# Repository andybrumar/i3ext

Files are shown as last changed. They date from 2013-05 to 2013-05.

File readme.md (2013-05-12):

Prusa i3 Extruder
-----------------

This is a derivative of Kliment's excellent work on his 'i3ext' project for
the Prusa i3 3D printer.

I have modified it to work with jhead hotends (potentially dual extrusion, 
if stacked vertically - option now available), MK7-compatible hobbed pulleys, and
variable mount hole spacings.  Example models are available for viewing in
the /STLs folder.

The extruder requires:

* NEMA17 stepper motor
* 625zz bearings (2 - for large gear axle)
* ~75mm M5 threaded rod (1 - for large gear axle)
* M5 nyloc (2 - for large gear axle)
* M5 nut (1 - for large gear axle)
* MK7 hobbed pulley (1 - Makerbot, TrinityLabs, etc)
* M3 nut (5 - 4-motor mount, 1-small gear)
* 6mm M3 screw (1 - small gear)

RP one of each:

* main_block_v2.scad -OR- main_block_v2_kliment.scad
* idler.scad
* large_gear, small_gear from gears.scad -OR- gears-kliment.scad
* fan_mount.scad

Kliment's variant uses smaller gear diameters, which makes the dual extruder 
less tall.

I have about 15 hours of printing with this extruder (non-Kliment) and it's been
reliable so far.

Build
=====

A great photo of how the assembly goes together can be found here:

http://www.flickr.com/photos/borgnamarco/8480383523/

Also check out the other photos in this photostream:

http://www.flickr.com/photos/borgnamarco/8481477322/in/photostream/

Large Gear:

1. Slip M5 nyloc into large gear.

2. Screw M5 threaded rod into backside of large gear and screw in until flush
with front of gear.

3. Screw M5 standard nut on other end until it butts up against large gear and tighten.

Extruder Body:

1. Slip 625zz bearings into slots at front and back of extruder body.

2. Slide M5 threaded rod assembly through front 625zz bearing.

3. Slide MK7 hobbed pulley onto M5 threaded rod.

4. Slide M5 threaded rod through back 625zz bearing.

5. Screw on M5 nyloc to the backside of the M5 threaded rod, locking the M5 threaded 
rod in place.

6. Align MK7 hobbed gear with filament channel and tighten set screw.

NEMA17 Motor: 

1. Align NEMA17 motor with motor mount holes.

2. Screw in four 6mm M3 screws to secure it to the extruder body.

Small Gear:

1. Slip M3 nut in small gear nut trap.

2. Screw in 6mm M3 nut into small gear side hole and screw through M3 nut.

3. Slide small gear on NEMA17 motor axle with teeth facing inward aligning the teeth
with the large gear.

Prusa i3 Carriage:

1. Screw extruder body into x-carriage holes.

Done!

Notes
====

* main_block_v2.scad: has config options to:

1. open up either the front, back, or both idler areas in case you want to stack and selectively use one drive area over the other (default = 'both')

2. adjust the x-carriage mount hole spacing (default = 30mm)

3. adjust the filament diameter (default = 3mm)

4. use either J-Head or Prusa Nozzle hotends (default = jhead)

5. select where you want the J-Head mount placed (default = 'both')

6. select whether you want the dual extruder (default = false)

NOTE: do NOT change the hobb diameter in the top of the config options as this
does not work right yet

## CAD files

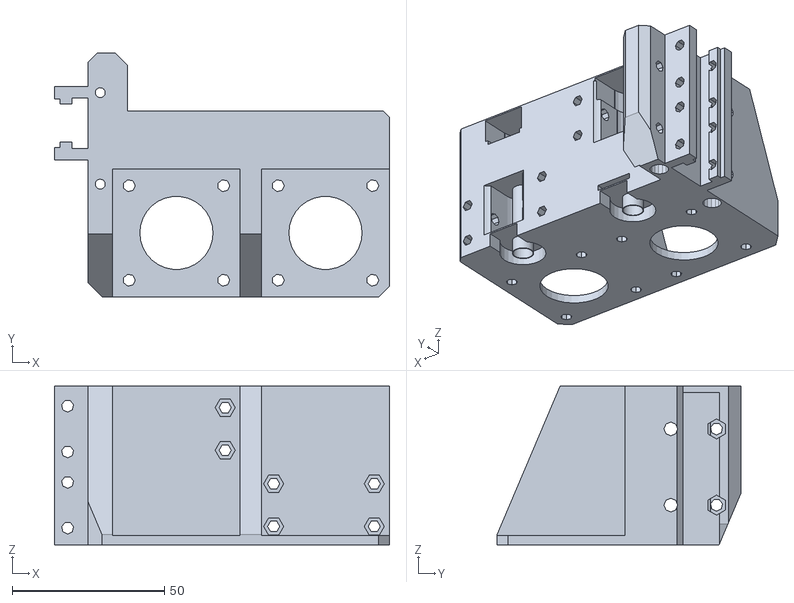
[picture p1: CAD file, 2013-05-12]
STLs/main_block_v2-dual.stl
109.9 x 80.0 x 52.0

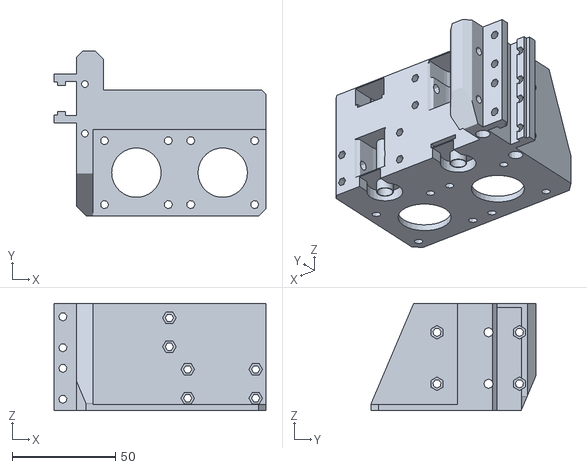
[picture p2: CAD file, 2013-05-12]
STLs/main_block_v2_dual_kliment.stl
102.9 x 80.0 x 52.0

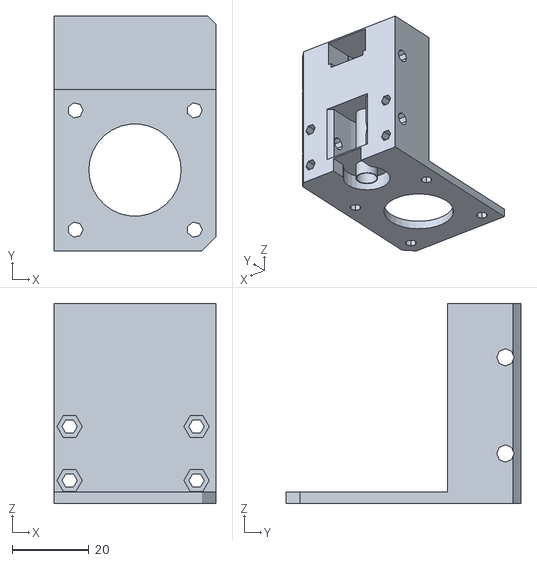
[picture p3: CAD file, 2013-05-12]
STLs/main_block_top_kliment.stl
42.0 x 61.0 x 52.0

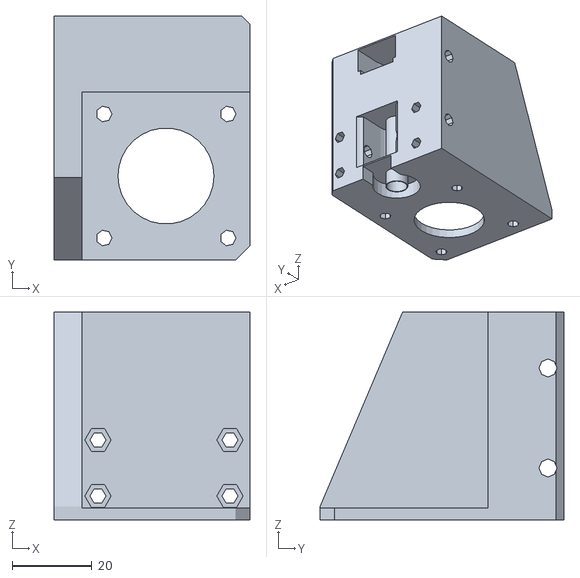
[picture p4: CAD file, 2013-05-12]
STLs/main_block_top.stl
49.0 x 61.0 x 52.0

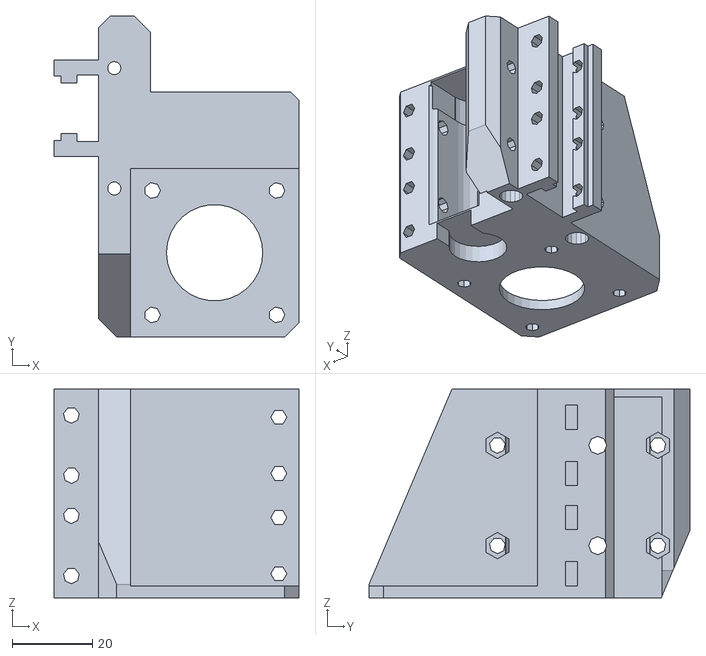
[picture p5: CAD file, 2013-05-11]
STLs/main_block_v2.stl
61.0 x 80.0 x 52.0

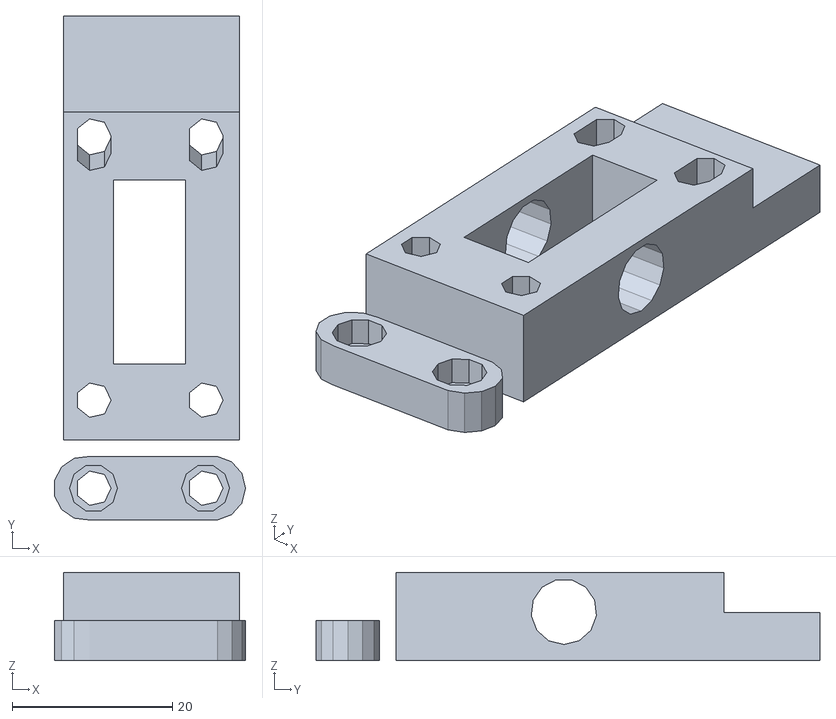
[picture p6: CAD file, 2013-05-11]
STLs/idler.stl
23.9 x 63.0 x 11.0

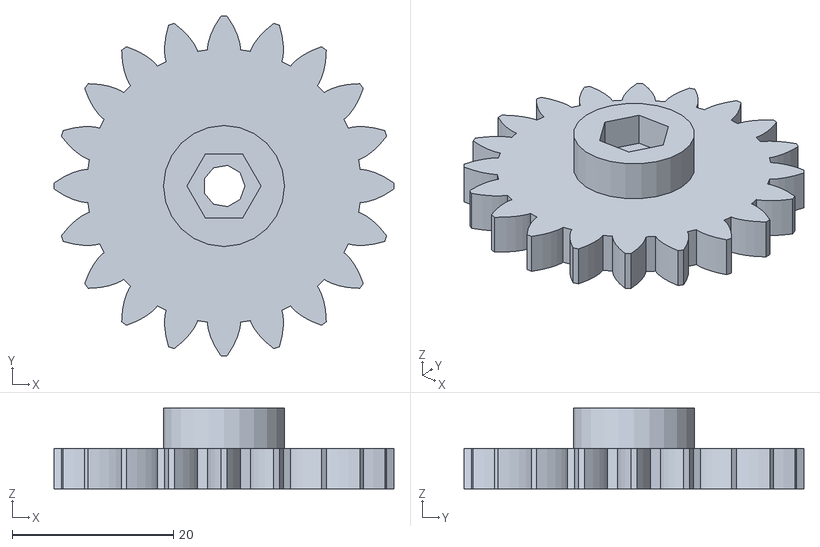
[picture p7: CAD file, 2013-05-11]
STLs/gears-large.stl
42.2 x 42.2 x 10.0

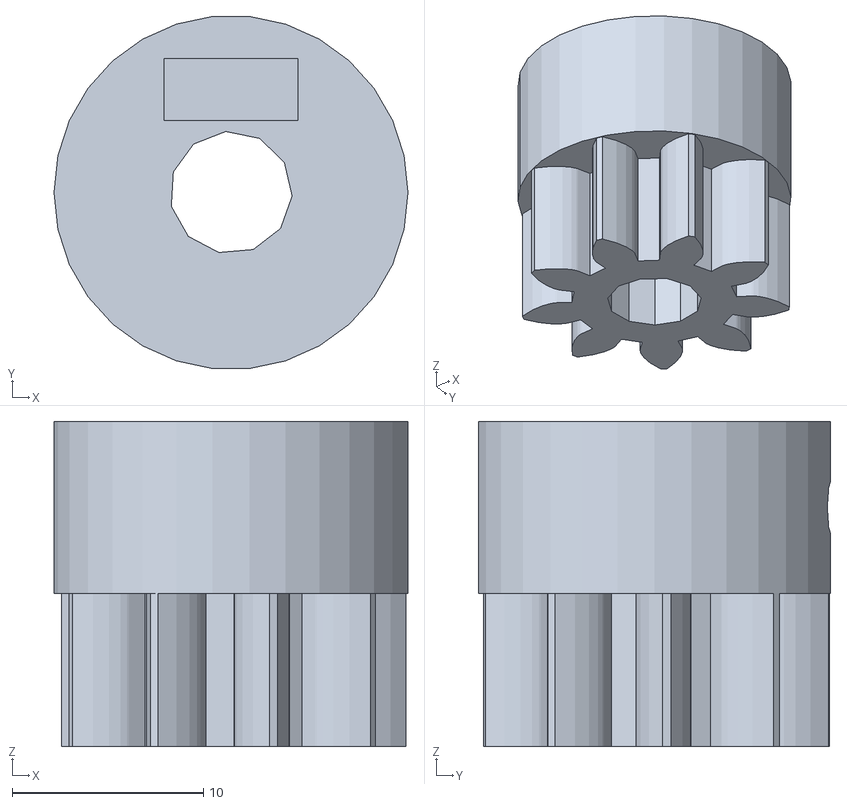
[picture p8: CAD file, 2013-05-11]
STLs/gears-small.stl
18.5 x 18.4 x 17.0

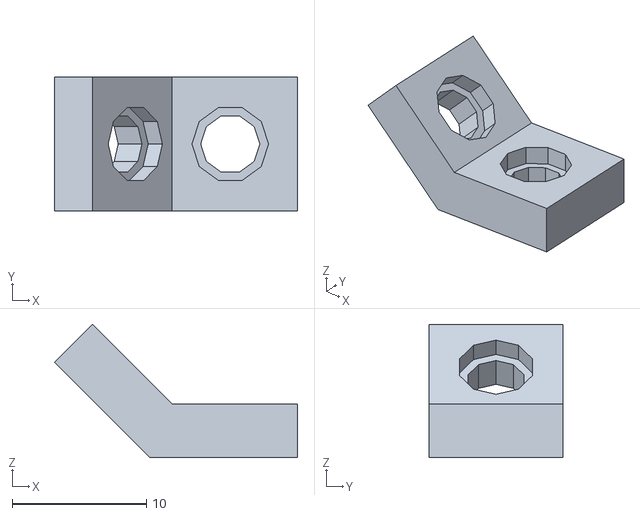
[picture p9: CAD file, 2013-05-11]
STLs/fan-mount.stl
18.1 x 10.0 x 9.90

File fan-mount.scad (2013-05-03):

// PRUSA iteration3
// Fan mount
// GNU GPL v3
// Josef Průša <iam@josefprusa.cz> and contributors
// http://www.reprap.org/wiki/Prusa_Mendel
// http://prusamendel.org

module fan_mount_base(){
 translate([0,0,0]) rotate([0,0,0]) cube([11,10, 4]);
 translate([0,0,0]) rotate([0,45,0]) translate([-10,0,0]) cube([10,10, 4]);
}

module fan_mount_holes(){
 translate([6,5,-1]) rotate([0,0,0]) cylinder(h=30, r=2.2, $fn=10);
 translate([6,5,2.5]) rotate([0,0,0]) cylinder(h=30, r=5.7/2, $fn=10);

 translate([0,5,0]) rotate([0,45,0]) translate([-5.5,0,-1]) cylinder(h=30, r=2.2, $fn=10);
 translate([0,5,0]) rotate([0,45,0]) translate([-5.5,0,2.5]) cylinder(h=30, r=5.7/2, $fn=10);
}

// Final part
module fan_mount(){
 difference(){
  fan_mount_base();
  fan_mount_holes();
 }
}

fan_mount();

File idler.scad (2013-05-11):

module extruder_idler_base(){
 translate([1.25,0,0]) cube([22,42+11,8+3]);
	
}

module extruder_idler_holes(){
 translate([12,21,0]){
  // Main cutout
  cube([9,23,25], center=true);
  // Idler shaft
  translate([-12,0,4.1+2])rotate([0,90,0])cylinder(r=4.1, h=24);
  // Screw holes
  translate([7,-16,-1]) cylinder(r=2.2, h=24);
  translate([-7,-16,-1]) cylinder(r=2.2, h=24);
  hull() {
    translate([7,17,-1]) cylinder(r=2.2, h=24);
    translate([7,17,-1]) rotate([10,0,0]) cylinder(r=2.2, h=24);
  }
  hull() {
    translate([-7,17,-1]) cylinder(r=2.2, h=24);
    translate([-7,17,-1]) rotate([10,0,0]) cylinder(r=2.2, h=24);
  }
 }
}


// Idler final part
module idler(){
 difference(){
  extruder_idler_base();
  extruder_idler_holes();
  translate([0,41,6]) cube(size=[25,20,10]);
 }
}

idler();
translate([0,-6,0]) screwholder();

module screwholder() {
	difference() {
		hull() {
			translate([4,0,0]) cylinder(r=4,h=5);
			translate([20,0,0]) cylinder(r=4,h=5);
		}
  		translate([5,0,-1])cylinder(r=2.2, h=24);
  		translate([19,0,-1])cylinder(r=2.2, h=24);
  		translate([5,0,2])cylinder(r=6/2, h=24);
  		translate([19,0,2])cylinder(r=6/2, h=24);
	}
}

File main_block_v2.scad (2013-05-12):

/*
bearing diameter 16mm
*/

hobb = 7; 					// use 6 if using Prusa's hobbed pulley - DOES NOT WORK!
mount_spacing = 30; 		// use 30 if using the newer, 30mm hole x-carriage
jhead_mount = true; 		// set to false if using prusanozzle or stacking
jhead_groove = "both";		// 'front', 'back', 'both', in case you
							// want to use a prusanozzle for 1 of 2 hotends
filament = 3.00;			// set to 3mm or 1.75mm or custom
							// note: a 1.5" gap is added to a filament channel
drive = "both";			// 'front' = front filament drive
							// 'back' = back filament drive
							// 'both' = both front and back
dual = false;				// dual extruder stacking?  ** EXPERIMENAL!!!!! **

// uncomment if printing
//rotate([0,0,-90]) translate([-45,7,0]) idler();
//rotate([0,0,0]) translate([45,-24,0]) idler();

// set filament radius
// add 1.5mm gap around filament holes through extruder body
filament_rad = filament/2 + 0.75; 

use <inc/jhead.scad>;		// http://www.thingiverse.com/thing:45379
use <inc/mk7.scad>; 		// TrinityLabs hobbed pulley
use <idler.scad>;           // idler
use <gears.scad>;           // gears
use <inc/nema17.scad>;		// NEMA17 stepper motor

if (dual==true) {
	translate([48.9,0,0]) import("STLs/main_block_top.stl");
	//translate([41.9,0,0]) import("STLs/main_block_top_kliment.stl");
}

// jhead mounting groove
module jhead() {
	%translate([2,0,12]) rotate([0,-90,0]) hotend_jhead(); 
	%translate([2,0,-13]) rotate([0,-90,0]) hotend_jhead(); 

	// jhead mount groove
	difference() {
		translate([-2,0,0]) cube(size=[9.5,24,52], center=true);
		cube(size=[5.6,16.5,52.1], center=true);
		translate([-4.8,0,0]) cube(size=[4.1,12.5,52.1], center=true);

		// M3 jhead clamping holes
		// front jhead hotend
		translate([-4.2,0,4.5]) rotate([90,90,0]) 
			cylinder(r=2, h=30, center=true);
		translate([-4.2,0,19.5]) rotate([90,90,0]) 
			cylinder(r=2, h=30, center=true);
		// back jhead hotend
		translate([-4.2,0,-20.5]) rotate([90,90,0]) 
			cylinder(r=2, h=30, center=true);
		translate([-4.2,0,-5.5]) rotate([90,90,0]) 
			cylinder(r=2, h=30, center=true);
	}
	// bottom bracing
	translate([-7.5,10,0]) cube(size=[2,4,52], center=true);
	translate([-7.5,-10,0]) cube(size=[2,4,52], center=true);
}

// filament path and prusanozzle mounting holes
module nozzlemount(){
	rotate([0,90,0]) translate([0,2,0]) cylinder(r=filament_rad, h=70); // filament cutout
	%rotate([0,90,0]) translate([0,2,-100]) 
		cylinder(r=filament_rad-0.75, h=200, $fn=30); // filament visual path
	// slightly coned filament entrance after MK7 hobbed pulley:
	rotate([0,90,0]) translate([0,2,17]) cylinder(r1=1, r2=3.5, h=8);
	//translate([1,0+2,0]) rotate([0,90,0]) cylinder(r1=4, r2=2, h=3);
	translate([0,15+2,0]) rotate([0,90,0]) cylinder(r=2, h=70);
	translate([10-2.8,15+2,0]) rotate([0,90,0]) cylinder(r=3.3, h=70,$fn=6);
	translate([0,-25+2,0]) rotate([0,90,0]) cylinder(r=2, h=70);
	translate([10-2.8,-25+2,0]) rotate([0,90,0]) cylinder(r=3.3, h=70,$fn=6);
}

// mk7 hobbed pulley - for visualization
if (drive=="back" || drive=="both") {
	%translate([21,9,36]) mk7();
}
if (drive=="front" || drive=="both") {
	%translate([21,9,15.5]) rotate([0,180,0]) mk7();
}

// idler - for visualization
if (drive=="back" || drive=="both") {
	%translate([0.5,30.5,50]) rotate([0,90,-90]) idler();
}
if (drive=="front" || drive=="both") {
	%translate([0.5,30.5,25]) rotate([0,90,-90]) idler();
}

// gears - for visualization
%rotate([0,180,90]) translate([-8,-21,2]) {
	big_gear();
	translate([0,0,-2]) small_gear();
	translate([0,0,-22]) cylinder(r=5/2, h=75, center=true); // M5 bolt
}
if (dual==true) {
	%rotate([0,180,90]) translate([-8,-70,2]) {
		big_gear();
		translate([0,0,-2]) small_gear();
		translate([0,0,-22]) cylinder(r=5/2, h=75, center=true); // M5 bolt
	}
}

// NEMA17 - for visualization
%translate([21,-21,3]) rotate([0,180,0]) nema17();
if (dual==true) {
	%translate([70,-21,3]) rotate([0,180,0]) nema17();
}

// construct the extruder body
difference(){
	union(){
		cube([42,19,52]);  							// drivetrain block
		translate([0,-42,0]) cube([42,42+3,3]);  		// NEMA17 motor mount
		translate([-7.99,-42,0]) cube([8,80,52]);  	// base
		translate([-1,31,0]) cube([6, 7, 52]);		// idler stop
		translate([-1,15,50]) cube([6, 20, 2]);		// back idler stop
		//translate([-1,15,22]) cube([6, 20, 2]);		// front idler stop

		// jhead mount
		if (jhead_mount) translate([-10.5,13+2,52/2]) jhead();
	} 

	// M5 bolt
	if (drive != "both") {
		translate([21,9-1,27]) cylinder(r=7/2, h=45, center=true, $fn=50);
	}

	// antiwarpagenation: angled corners
	if (dual==false) {
		translate([46,-91,-1]) rotate([0,0,45]) cube(40); // top left NEMA mount corner
		translate([46,13,-1]) rotate([0,0,45]) cube([40,40,60]); // top-right corner
	}
	translate([-11,-91,-1]) rotate([0,0,45]) cube([40,40,60]);
	translate([-12,31,-1]) rotate([0,0,45]) cube([20,20,60]);
	translate([6,33,-1]) rotate([0,0,45]) cube([40,40,60]);

	// NEMA 17 motor circle cutout and mounting holes
	translate([21,-21,-1]) cylinder(r=12, h=5);
	translate([21+15.5,-21+15.5,-1]) cylinder(r=2, h=5);
	translate([21+15.5,-21-15.5,-1]) cylinder(r=2, h=5);
	translate([21-15.5,-21+15.5,-1]) cylinder(r=2, h=5);
	translate([21-15.5,-21-15.5,-1]) cylinder(r=2, h=5);

	// idler bearing cutout from drivetrain block
	// may not be needed - at least for 3mm filament!
	// problems pushing filament into bottom hole w/ this cutout there
	if (drive=="back" || drive=="both") {
		translate([21,24+3,25.5]) cylinder(r=12, h=25);
	}
	if (drive=="front" || drive=="both") {
		translate([21,24+3,5.5]) cylinder(r=12, h=20);
	}

	// hobbed pulley cutout from drivetrain block
	if (drive=="back" || drive=="both") {
		translate([21,8.1,25.5]) cylinder(r=hobb, h=25); 
		translate([-6+20,8,25.5]) cube([14,12,25]); 
		translate([21,8.1,5.5]) cylinder(r=hobb, h=2); // support for bearing
		translate([-6+20,8,5.5]) cube([14,12,2]); // support for back bearing 
	}
	if (drive=="front" || drive=="both") {
		translate([21,8.1,5.5]) cylinder(r=hobb, h=20); 
		translate([-6+20,8,5.5]) cube([14,12,20]);  
		translate([21,8.1,41.5]) cylinder(r=hobb, h=2); // support for bearing
		translate([-6+20,8,41.5]) cube([14,12,5]); // support for back bearing
	}

	// remove excess jhead mounting rails
	if (jhead_groove=="front") {
		translate([-20,0,26]) cube(size=[12,30,27]);
	} else if (jhead_groove=="back") {
		translate([-20,0,-5]) cube(size=[12,30,27]);
		translate([-15,0,12]) rotate([0,-55,0]) cube(size=[12,30,15]);
	} 

	// 625zz filament drive bearing cutouts from drivetrain block
	translate([21,9-0.9,-1]) cylinder(r=8.1, h=6); 
		%translate([21,9-0.9,-1]) cylinder(r=8.1, h=5); // visualize it
	translate([21,9-0.9,-5+52-4]) cylinder(r=8.1, h=8.5); 
		%translate([21,9-0.9,-5+52-4]) cylinder(r=8.1, h=5); // visualize it

	// filament drive bearing insert cutouts from drivetrain block
	translate([13,8,43]) cube([16.2,20,8.5]);
	translate([-6+21,8,-50+5]) cube([12,12,50]);

	//mounting holes for x-carriage mount from base
	translate([-4,22+(mount_spacing-24)/2,-28]){
		translate([0,0,0]) rotate([0,0,0]) 
			cylinder(r=3.3, h=70, $fn=15);
		translate([0,0-mount_spacing,0]) rotate([0,0,0]) 
			cylinder(r=3.3, h=70, $fn=15);
		translate([0,0,30]) rotate([0,0,0]) 
			cylinder(r=3.3/2, h=70, $fn=15);
		translate([0,0-mount_spacing,30]) rotate([0,0,0]) 
			cylinder(r=3.3/2, h=70, $fn=15);
	}

	// idler nuts and filament channels from drivetrain block and base
	translate([0,0,-2]){
		// PrusaNozzle mount holes
		translate([-10,2+8+4-1,52-12]) nozzlemount();
		translate([-10,2+8+4-1,52-12-25]) nozzlemount();

		// idler nuts
		if (drive=="back" || drive=="both") {
			translate([37,12,52-12-7]) rotate([90,0,0]) cylinder(r=3.3, h=12.1,$fn=6);
			translate([37,12,52-5]) rotate([90,0,0]) cylinder(r=3.3, h=12.1,$fn=6);
		}
		if (drive=="front" || drive=="both") {
			translate([37,12,52-12-7-25]) rotate([90,0,0]) cylinder(r=3.3, h=12.1,$fn=6);
			translate([37,12,52-5-25]) rotate([90,0,0]) cylinder(r=3.3, h=12.1,$fn=6);
		}

		// idler bolts
		if (drive=="back" || drive=="both") {
			translate([5+32,-1,52-12+7]) rotate([0,90,90]) 
				rotate([0,0,30]) cylinder(r=2, h=40, $fn=6);
			translate([5+32,-1,52-12-7]) rotate([0,90,90]) 
				rotate([0,0,30]) cylinder(r=2, h=40, $fn=6);
		}
		if (drive=="front" || drive=="both") {
			translate([5+32,-1,52-12-25+7]) rotate([0,90,90]) 
				rotate([0,0,30]) cylinder(r=2, h=40, $fn=6);
			translate([5+32,-1,52-12-25-7]) rotate([0,90,90]) 
				rotate([0,0,30]) cylinder(r=2, h=40, $fn=6);
		}

		// pretty cutout - angled idler area corners
		translate([-10,30,0]) rotate([-23,0,0]) cube([20,12,50]);
		translate([0,27,-3]) rotate([0,23,0]) cube([20,12,50]);

		// pretty cutout - angled base underneath NEMA17 motor
		translate([-10,-66,0]) rotate([-23,0,0]) cube([12,20,90]);
		}
	}

// M5 bolt support
if (drive != "both") {
	difference() {
		translate([21,9-1,13]) cylinder(r=7.5/2, h=26, center=true, $fn=50);
		translate([21,9-1,13]) cylinder(r=7/2, h=27, center=true, $fn=50);
	}
}

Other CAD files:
main_block_v2_kliment.scad
depreciated/main_block.scad
gears-kliment.scad
gears.scad
inc/jhead.scad
inc/mk7.scad
inc/nema17.scad

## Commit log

2013-03-28 updated for jhead
    LOTS of changes!
    [main_block.scad]
2013-03-28 added idler(s) for printing a plate
    [main_block.scad]
2013-03-28 moved small gear slightly in render
    [main_block.scad]
2013-03-28 initial commit
    from
    https://github.com/tkramm/galileo/blob/master/components/nema17.scad
    [nema17.scad]
2013-03-28 added NEMA17 for visualization
    had to move gears slightly to line up better as well
    [main_block.scad]
2013-03-28 forgot to make gears opaque in last commit
    [main_block.scad]
2013-03-28 changed jhead_mount comment slightly
    [main_block.scad]
2013-03-29 moved xcarriage mounting holes up 1mm
    did this b/c w/ 30mm hole spacing, one of the holes impacts the jhead
    mount. moving it up puts a little material between it to make it more
    rigid.
    [main_block.scad]
2013-03-29 initial commit
    added config options to allow drive area selection - front or back
    [main_block_v2.scad]
2013-03-29 fixed 625zz bearing spacing - was off by ~1mm
    [main_block.scad]
2013-03-29 default to rendering both front and back drives
    [main_block_v2.scad]
2013-03-29 moved hobbed pulley cutout back 1mm
    found hobbed pulley area needed moved 1mm closer to the motor in order
    to line up properly with gears
    [main_block_v2.scad]
2013-03-29 moved hobbed pulley area closer to motor by 1mm
    found it wasn't centered with the pulleys
    [main_block.scad]
2013-03-29 adjusted per josefprusa's settings
    more teeth on large gear, less teeth on small gear. nut trap and screw
    hole added on small gear.
    [gears.scad]
2013-03-30 adjusted small gear bore, nut trap
    defaults were too small. adjusted them upward a bit.
    [gears.scad]
2013-04-01 added nut trap and set screw
    gear ratios are identical to kliment's defaults
    [gears-kliment.scad]
2013-04-01 minor update to large gear bore and nut diameter
    [gears.scad]
2013-05-03 mount to jhead screw with an M3 bolt
    [fan-mount.scad]
2013-05-03 updated with thumb tab for easier filament removal
    [idler.scad]
2013-05-10 moved bearing cutout out slightly; coned filament entrance slightly
    [main_block_v2.scad]
2013-05-10 increased mount hole spacing to 30mm
    [main_block_v2.scad]
2013-05-11 now can config filament diameter in scad
    [main_block_v2.scad]
2013-05-11 added photo link for assembly
2013-05-11 initial commit of stls
    [fan-mount.stl, gears-large.stl, gears-small.stl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]
2013-05-11 added config for jhead mount location
    [main_block_v2.scad]
2013-05-11 moved stl models to STLs folder
    [fan-mount.stl, gears-large.stl, gears-small.stl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]
2013-05-11 moved jhead.scad, mk7.scad, nema17.scad to /inc folder
    [jhead.scad, main_block_v2.scad, mk7.scad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]
2013-05-11 moved v1 of main_block.scad to /depreciated
    [main_block.scad]
2013-05-11 config option for jhead mount placement
2013-05-11 added bottom idler holes back
    [idler.scad, idler.stl]
2013-05-12 dual extrusion
    [main_block_top.stl, main_block_top_kliment.stl]
2013-05-12 added dual extrusion option
    [main_block_v2.scad]
2013-05-12 extruder body using kliment's gears, which have a lower gear ratio and smaller diameter allowing for the stacked, dual extruder option
    allows this to be less tall than the other with larger gear diameters.
    [main_block_v2_kliment.scad]
2013-05-12 dual extruder examples
    [main_block_v2-dual.stl, main_block_v2_dual_kliment.stl]
2013-05-12 updated with dual extrusion option
2013-05-12 latest dual extruder example using larger gears
    [main_block_v2-dual.stl]
